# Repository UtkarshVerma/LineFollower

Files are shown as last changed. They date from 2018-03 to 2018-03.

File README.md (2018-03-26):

# Line Follower 

The front view

[**Line Follower Test Video on YouTube**](https://youtu.be/Ljhs3s-MkIQ)

This repository contains the relevant files for a Line Follower I made. It is based on PIC16F84A and is somewhat inherited from this great [instructable](https://www.instructables.com/id/Line-Follower-Robot/) by **Mohammad Yousefi**. I've also added his original instructions as a rar named "Mohammad Yousefi Resources" to this repo.
I'd like to add that the schematic file is built using [Proteus](https://www.labcenter.com/) and most of the boards have also been designed using it, except for the extension PCBs, which have been designed using [eagleCAD](https://www.autodesk.com/products/eagle/overview).

---
## The Differences
The robot I made differs by large from the one made in the instructable. So **you'll have to be a bit careful** if you're thinking of merging both these projects. The differences are as follows:
* I wanted to use Lithium-ion batteries to power this robot up, so I dropped the whole messy AA battery system;
* I've used a Chinese motor driver named **Mini L298 Motor Driver** rather than the **bulky L298 module or IC**. Luckily there's already an [instructable](https://www.instructables.com/id/Tutorial-for-Dual-Channel-DC-Motor-Driver-Board-PW/#discuss) for it.
    > However, there's no issue since the input mechanisms are identical in both, except for **PWM**.
* I've integrated the battery connection toggler, [**Boggler**](https://www.instructables.com/id/Battery-Connection-TogglerSeries-Parallel-Boggler/) in my project to enable clean and easy toggling between charging and usage modes.
* I've made the PCBs **detachable** using connectors and extension PCBs. This aids further modification of the robot, so you can build upon it easily in the future.
* The inner part of this robot has been left intentionally empty for **allowing the addition of more circuits**.
* The code for this robot has been worked up from scratch in **C programming language**, and due to this the line detection algorithm is also different.
* There's **no PWM functionality in the original code** posted in the instructable, so I added it in my code for implementing speed control for the motors to **allow a variety of motors** to work with this project.
* Instead of ironing the toner onto the top side of PCB for the silkscreen, I've pasted a white paper printed with the **mirrored silkscreen**.

---
## The Code
The code is written in **C** as stated earlier. It has been written to allow easy modification through variable values. The configuration variables are stated below:
1. `normPWM` : The PWM duty for **forward motion**.
2. `fastPWM` : The PWM duty for **extreme turns**.
3. `slowPWM` : The PWM duty for **slow turns**.

Modifying these values affects the motor speed during their respective phases. There are other variables as well, you may modify them by referring to the code comments.

### Algorithm
To detect lines, this robot does the following:
1. Store the value of the middle sensor in `lColour` to detect the line colour accordingly.
    **0 - Black line, 1 - White line**.
2. Begin forward motion.
3. If one sensor on either side(i.e. left or right sensor) strays off and its value differs from `lColour`, then **slow turns** have to be made towards the opposite side.
4. If one sensor on either side strays off and its value equals to `lColour`, then **extreme turns** are to be made towards the opposite site.
5. If the front sensor and a sensor on either side strays off, then a **perpendicular turn** is detected, so the robot spins in the corresponding direction. The thing to be noted here is that no the motors run at full speed during this phase and no PWM is used.

When the mode switching button is pressed and custom mode is enabled, the robot **reads last state values from the EEPROM** of PIC16F84A. While exiting the custom mode, it also **writes the contemporary state values to the EEPROM**. The memory locations used for this purpose are stated below:
* `0x00` - Stores whether the robot was turned off during custom or default mode.
* `0x01` - Stores the last settings of the left motor in custom mode.
* `0x02` - Stores the last settings of the right motor in custom mode.

This concludes the code section. I won't be going more into the code details since more than sufficient comments have been made there.

---
## Some Notes
Though there aren't much, here are some things you have to look out for while making this project:
* The motor driver used is different so **you can abandon the back PCB** if you wish. I have wired up mine using wires alone and pasted the module onto the PCB onto the back PCB using glue.
* The extension PCBs have to be well soldered with their respective boards since they undergo huge stress while detaching the PCBs.
* The extension PCBs also serve as **PCB-jumpers** to avoid the jumpers between the top and bottom boards. So, you'll have to make the jumper connection through these extension boards so as to allow the detaching of boards.

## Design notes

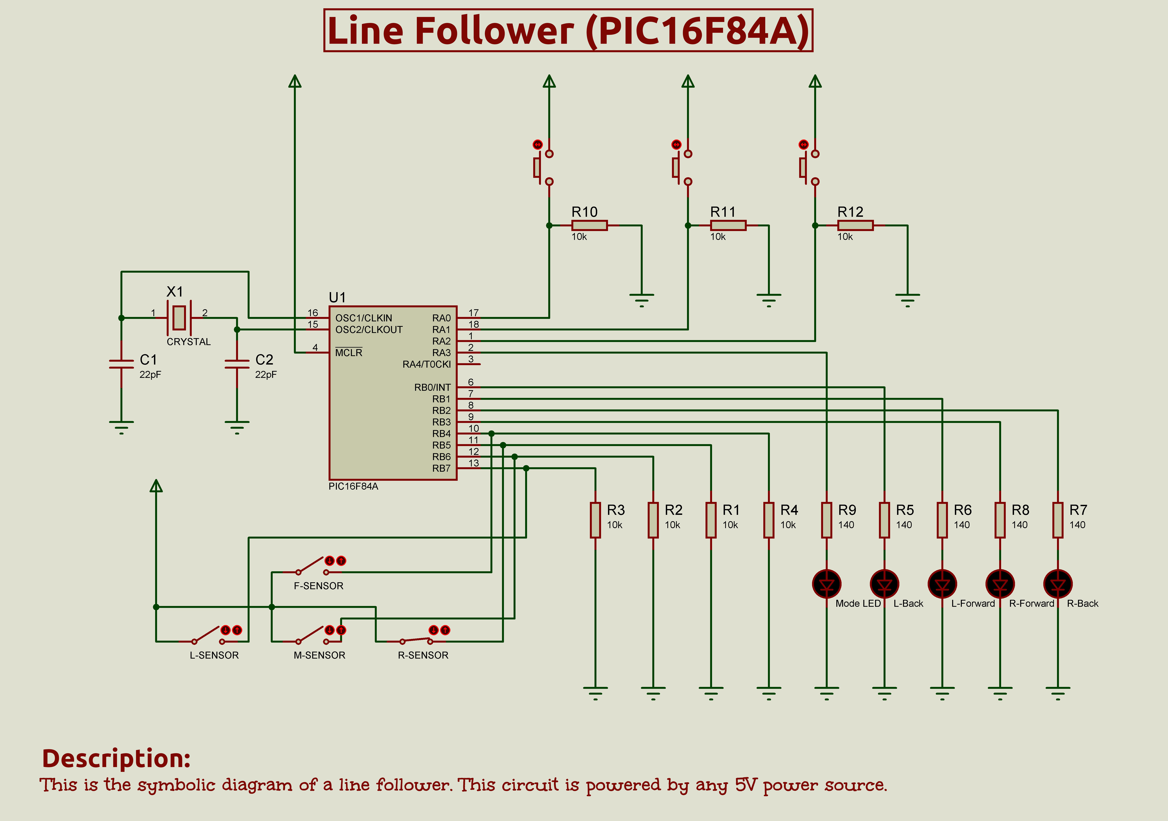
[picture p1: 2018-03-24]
Schematic + Simulation/Schematic.jpg

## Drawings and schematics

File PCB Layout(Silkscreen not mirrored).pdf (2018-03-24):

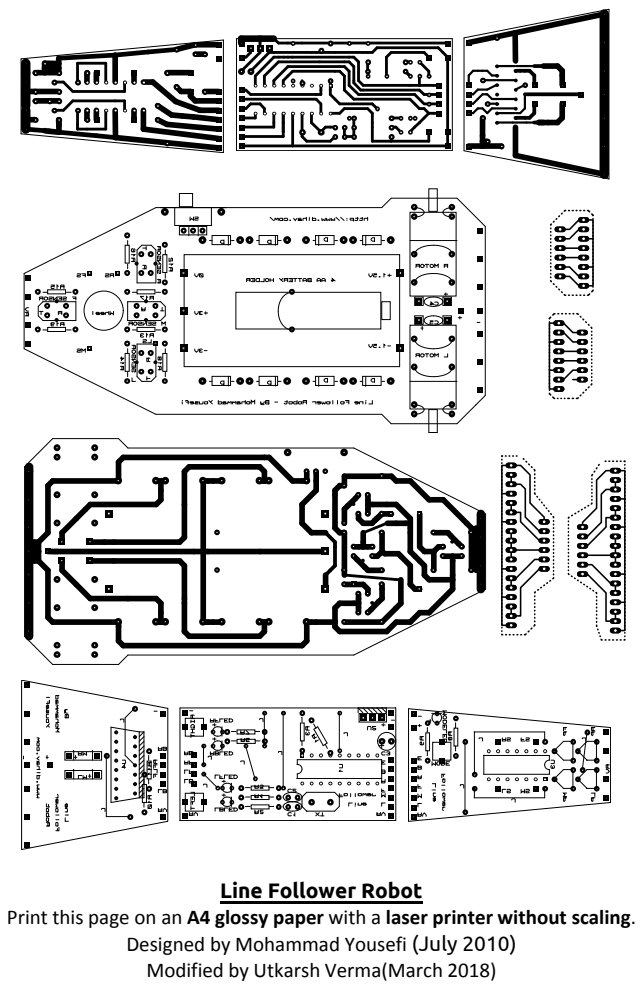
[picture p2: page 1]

Print this page on an A4 glossy paper with a laser printer without scaling.

Designed by Mohammad Yousefi (July 2010)
Modified by Utkarsh Verma(March 2018)

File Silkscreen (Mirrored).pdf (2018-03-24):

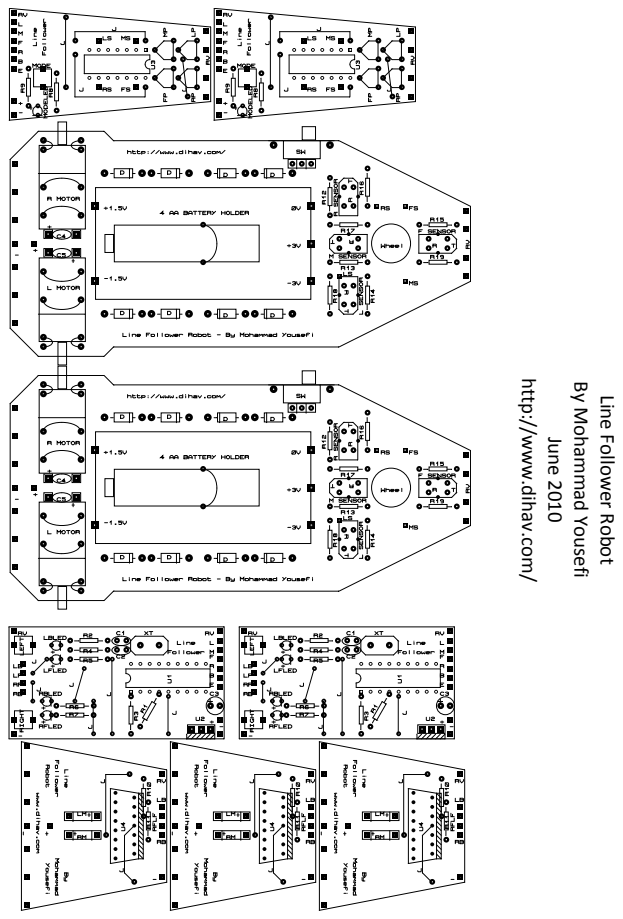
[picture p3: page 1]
June 2010

http://www.dihav.com/

By Mohammad Yousefi

Line Follower Robot

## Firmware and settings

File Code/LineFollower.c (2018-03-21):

/*
 * File:   LineFollower.c
 * Author: Utkarsh Verma
 * Created on March 20, 2018
 * Description: Hi-Tech C line follower  program for PIC16F84A.
 */
//===================================================================================
/*CONFIG*/
#pragma config FOSC = HS        // HS oscillator
#pragma config WDTE = OFF       // Watchdog Timer disabled
#pragma config PWRTE = ON       // Power-up Timer enabled
#pragma config CP = OFF         // Code protection disabled
//-------------------------------------------------------------
#include <htc.h>
#define _XTAL_FREQ 4000000      //Using a 4MHz Crystal Oscillator
//-------------------------------------------------------------
/*Pin definitions*/
#define MBtn RA0                //Mode button
#define lBtn RA1                //Left motor button
#define rBtn RA2                //Right motor button
#define MLED RA3                //Mode LED

#define lMtrB RB0               //Left motor backward
#define lMtrF RB1               //Left motor forward
#define rMtrB RB2               //Right motor backward
#define rMtrF RB3               //Right motor forward

#define fSen RB4                //Front sensor
#define rSen RB5                //Right sensor
#define mSen RB6                //Middle sensor
#define lSen RB7                //Left Sensor
//-------------------------------------------------------------
/*PWM duty cycles*/
#define normPWM 170     //PWM duty while moving forward
#define slowPWM 180     //PWM duty while turning slowly
#define fastPWM 220     //PWM duty motors while turning fast
//-------------------------------------------------------------
/*Global variables*/
int phase = 1;          //PWM duty phase
int lFwd = 0, rFwd = 0;     //Motion states
int rFirst = 1, lFirst = 1; //Check for first iteration
int lColour = 1;        //Stores line colour, 1 - White, 0 - Black
int count;          //Counts the number of PWM enabled outputs
int PWM;
//===================================================================================
/*PWM generation*/
void interrupt ISR(void)
{
    if(T0IF)
    {
        if(phase)    //HIGH phase
        {
            TMR0 = PWM;    //Time the duty phase
            if(lFwd && rFwd)    //Time the duty phase second time
                TMR0 = PWM;
            if(lFwd)lMtrF = 0;
            if(rFwd)rMtrF = 0;
            phase=0;    //Switch to LOW phase
        }
        else     //LOW phase
        {
            TMR0 = 255 - PWM;  //Time the rest of the phase
            if(lFwd && rFwd)   //Time the rest of the phase second time
                TMR0 = 255 - PWM;
            if(lFwd)lMtrF = 1;
            if(rFwd)rMtrF = 1;
            phase=1;   //Switch to HIGH phase
        }
        T0IF = 0;     //Clear the interrupt
    }
}
//===================================================================================
/*PWM implementation to pins*/
void updatePWM(void)
{
    if(rFwd && lFwd && (lFirst || rFirst)) T0IE = 1;
    if(lFwd)
    {
        if(lFirst)    //If first iteration
        {
            if(!rFwd)  //If no rMtrF PWM generation
                T0IE = 1;   //Enable timer0 interrupt
            lFirst = 0;    //The later iterations won't be the first
        }
    }
    else
    {
        if(!lFirst)   //If not first iteration
        {
            lMtrF = 0; //Set lMtrF back to LOW
            lFwd = 0;  //Disable further PWM generation for rMtrF
            if(!rFwd)  //If no rMtrF PWM generation
                T0IE = 0;   //Enable timer0 interrupt
            lFirst = 1;    //The next iteration will be the first
        }
    }
    if(rFwd)
    {
        if(rFirst)    //If first iteration
        {
            if(!lFwd)  //If no lMtrF PWM generation
                T0IE = 1;   //Enable timer0 interrupt
            rFirst = 0;    //The later iterations won't be the first
        }
    }
    else
    {
        if(!rFirst)   //If not first iteration
        {
            rMtrF = 0; //Set rMtrF back to LOW
            rFwd = 0;  //Disable further PWM generation for rMtrF
            if(!lFwd)  //If no lMtrF PWM generation
                T0IE = 0;   //Disable timer0 interrupt
            rFirst = 1;    //The next iteration will be the first
        }
    }
}
//===================================================================================
/*Sets the motor outputs to LOW*/
void flushMotor(int n)
{
    switch(n)
    {
        case 0:   //Flush backward outputs
            lMtrB = 0; rMtrB = 0;
            break;
        case 1:   //Flush forward outputs
            lMtrF = 0; rMtrF = 0;
            break;
        case 2:   //Flush all outputs
            lMtrB = 0; rMtrB = 0;
            lMtrF = 0; rMtrF = 0;
    }
}
//===================================================================================
/*Updates the motor outputs*/
void updateMotor(int n)
{
    switch(n)
    {
        case 0:   //Update left motor
            lMtrF = (((int)eeprom_read(2)) != 1)?1:0;
            lMtrB = (((int)eeprom_read(2)) != 0)?1:0;
            break;
        case 1:   //Update right motor
            rMtrF = (((int)eeprom_read(1)) != 1)?1:0;
            rMtrB = (((int)eeprom_read(1)) != 0)?1:0;
            break;
        case 2:   //Update both motors
            lMtrF = (((int)eeprom_read(2)) != 1)?1:0;
            lMtrB = (((int)eeprom_read(2)) != 0)?1:0;
            rMtrF = (((int)eeprom_read(1)) != 1)?1:0;
            rMtrB = (((int)eeprom_read(1)) != 0)?1:0;
    }
}
//===================================================================================
/*The main set of tasks*/
void main()
{
    lColour = mSen;
    /*Set pin type*/
    TRISA = 0b10111;
    TRISB = 0b11110000;

    /*PWM initialization*/
    OPTION_REG &= 0xC0;     //Set prescaler to 1:2
    GIE = 1;            //Enable global interrupts

    /*Restore last state*/
    MLED = (int)eeprom_read(0);
    if(MLED)
        updateMotor(2);
    else
    {
        PWM = normPWM;
        lFwd = 1; rFwd = 1;
        updatePWM();
    }

    /*Motor button push counters*/
    int lmbCount, rmbCount;

    while(1)    //Infinite loop
    {
        /*Default mode*/
        if(!MLED)
        {
            if(fSen == mSen)
            {
                flushMotor(0);    //No backward motion
                if(lSen == rSen)  //Move forward
                {
                    PWM = normPWM;
                    lFwd = 1;
                    rFwd = 1;
                }
                else  //Robot straying off track
                {
                    PWM = (mSen == lColour)?slowPWM:fastPWM; //Speed adjustment based on type of turn
                    if(rSen == lColour)    //Turn right
                    {
                        lFwd = 1;
                        rFwd = 0;
                    }
                    else   //Turn left
                    {
                        lFwd = 0;
                        rFwd = 1;
                    }
                }
            }
            /*Extreme turns*/
            else
            {
                lFwd = 0; rFwd = 0;
                if(rSen == lColour)   //Turn right
                {
                    lMtrF = 1; rMtrF = 0;
                    lMtrB = 0; rMtrB = 1;
                }
                else  //Turn left
                {
                    lMtrF = 0; rMtrF = 1;
                    lMtrB = 1; rMtrB = 0;
                }
            }
            updatePWM();
        }
        //-------------------------------------------------------------
        /*Mode switching*/
        if(MBtn)
        {
            /*Change mode*/
            MLED = !MLED;
            eeprom_write(0,MLED);
            if(MLED)    //If turning custom mode on
            {
                T0IE = 0;    //Stop PWM
                /*Load last states*/
                rmbCount = (int)eeprom_read(1);
                lmbCount = (int)eeprom_read(2);

                updateMotor(2);  //Change both motor states
            }
            else    //If turning custom mode off
            {
                flushMotor(2);
                PWM = normPWM;
                lFirst = 1; rFirst = 1;  //For updatePWM()
                lFwd = 1; rFwd = 1;
            }
            __delay_ms(500);    //Delay for button press
        }
        //-------------------------------------------------------------
        /*Motor button actions*/
        if(MLED)
        {
            if(lBtn)    //Left button is pressed
            {
                lmbCount++;
                lmbCount%=3;
                eeprom_write(2,lmbCount);   //Save last states
                updateMotor(0);     //Change left motor state
                __delay_ms(500);    //Delay for button press
            }
            if(rBtn)    //Right button is pressed
            {
                rmbCount++;
                rmbCount%=3;
                eeprom_write(1,rmbCount);   //Save last state
                updateMotor(1);     //Change right motor state
                __delay_ms(500);    //Delay for button press
            }
        }
        //-------------------------------------------------------------
    }
}
//===================================================================================
